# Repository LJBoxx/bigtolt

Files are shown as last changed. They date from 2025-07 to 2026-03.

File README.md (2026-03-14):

# BigTOLT - Big(kinda) esc with TOLT mosfets

18 mosfet TOLT package esc design based off vesc6 schematic and compatible with [VESC](https://github.com/vedderb/bldc) firmware.

There is also a small high voltage converter used for higher voltage operation, aim was to have a quite big voltage operation range. But if you will test it with high voltage, please do mind that the voltage sensing is **un-isolated**

# Untested !!
This board is not tested but the pcb is ready for prototype. BOM and gerber are in [here](/tolt)

## Board preview
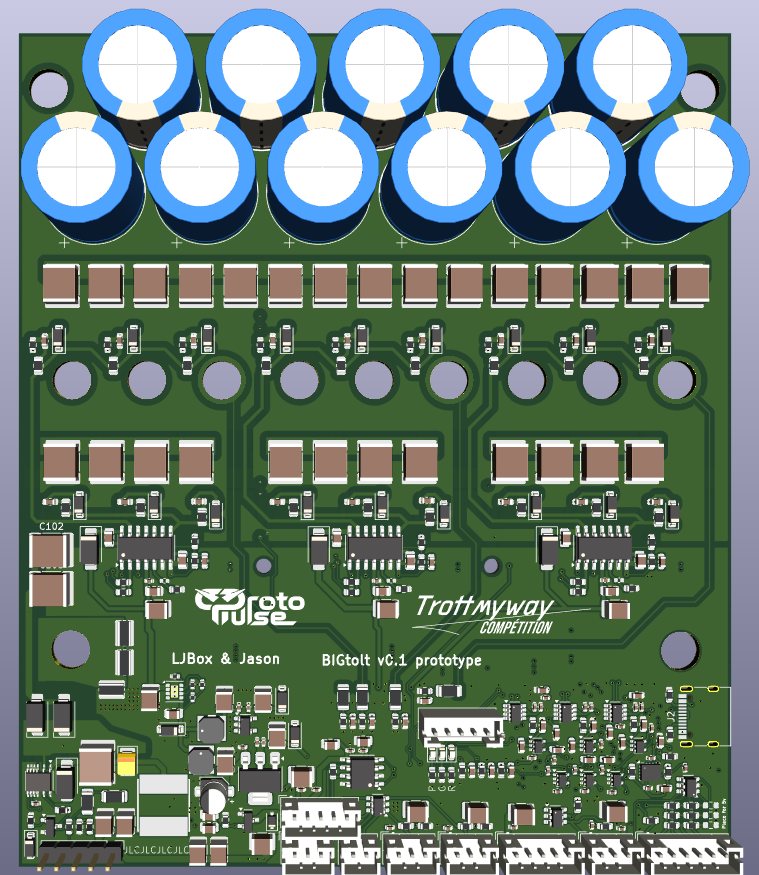
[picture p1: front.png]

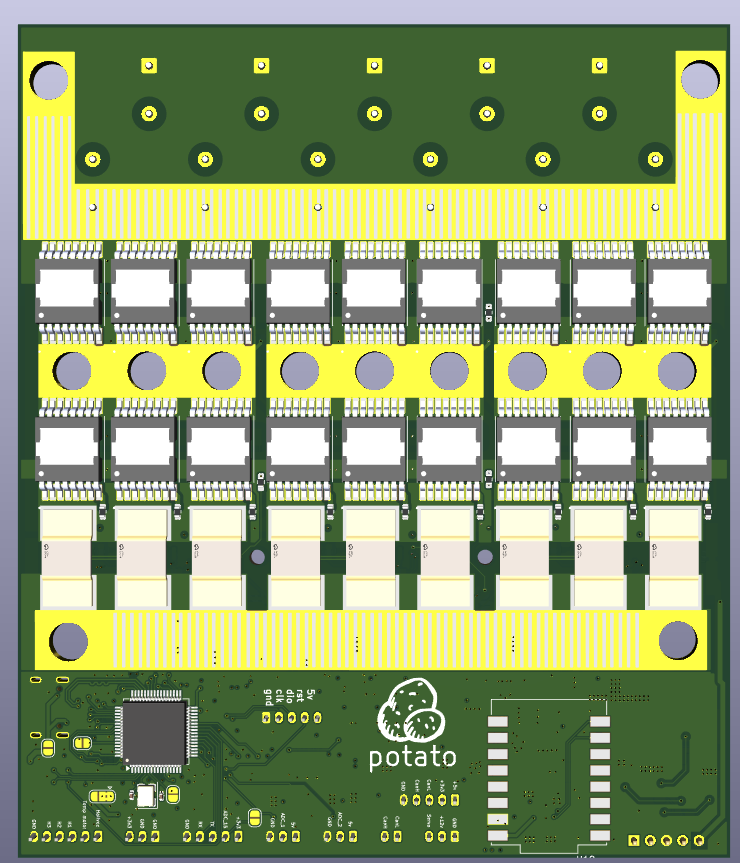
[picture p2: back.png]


## Liability
This project sources are provided **as is** therfore I, and the co controbutors to this repository shall not be held responsible for any damage occured, including but not limited to hardware damages or other physical injury caused by the outcomes of this source. **You are responsible for your actions. If used wrong, it will go wrong!**

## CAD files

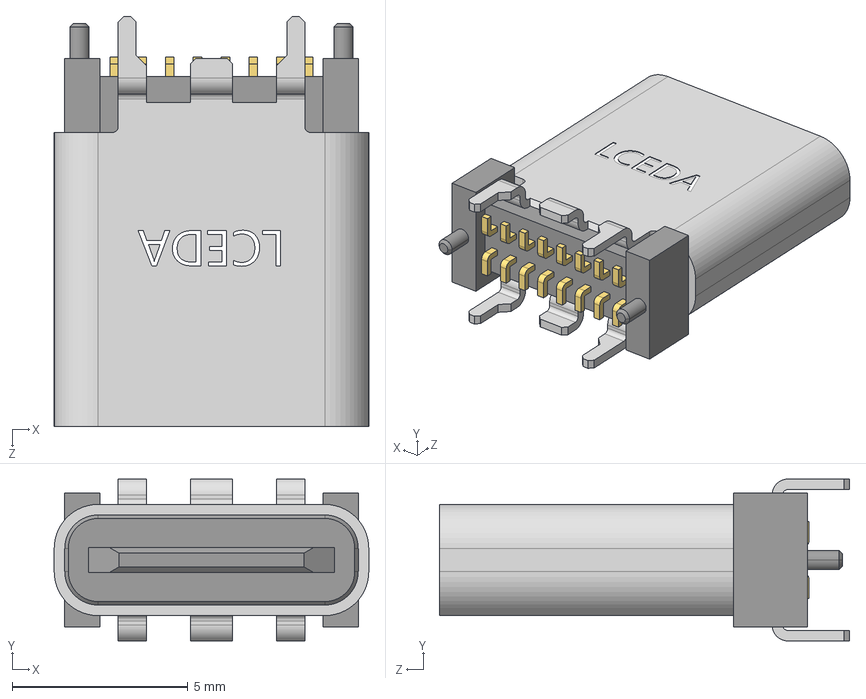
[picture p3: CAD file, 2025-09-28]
tolt/3d/USB-C-SMD_GT-USB-7051A.step
8.94 x 4.60 x 11.7 mm

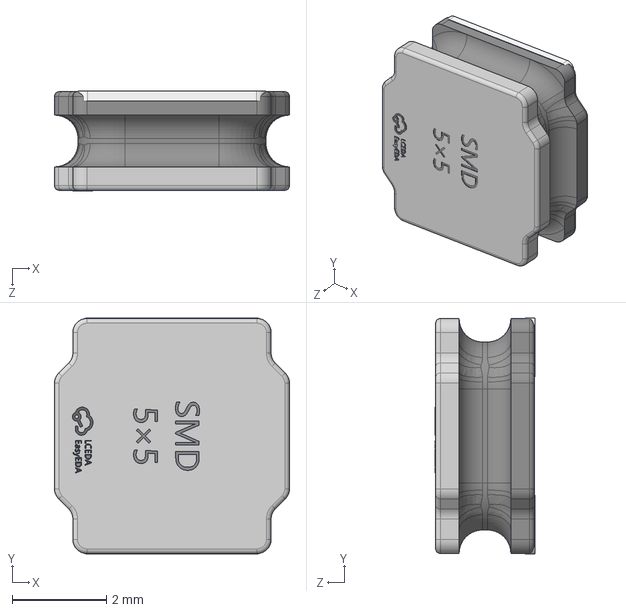
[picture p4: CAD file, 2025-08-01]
tolt/3d/IND-SMD_L5.0-W5.0-H2.1.step
5.00 x 5.02 x 2.12 mm

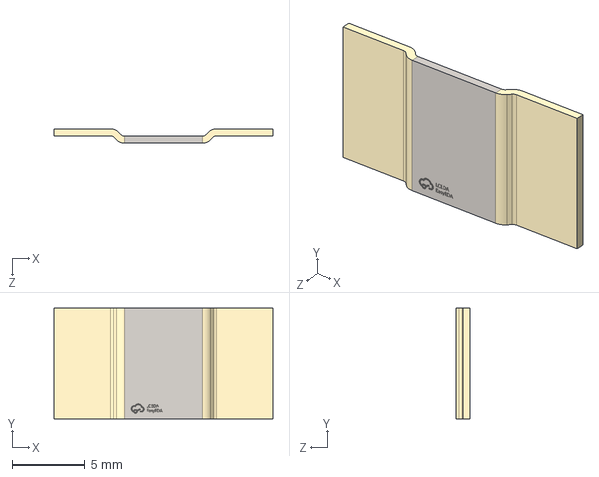
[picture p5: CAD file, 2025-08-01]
tolt/3d/R5930.step
15.0 x 7.60 x 0.981 mm

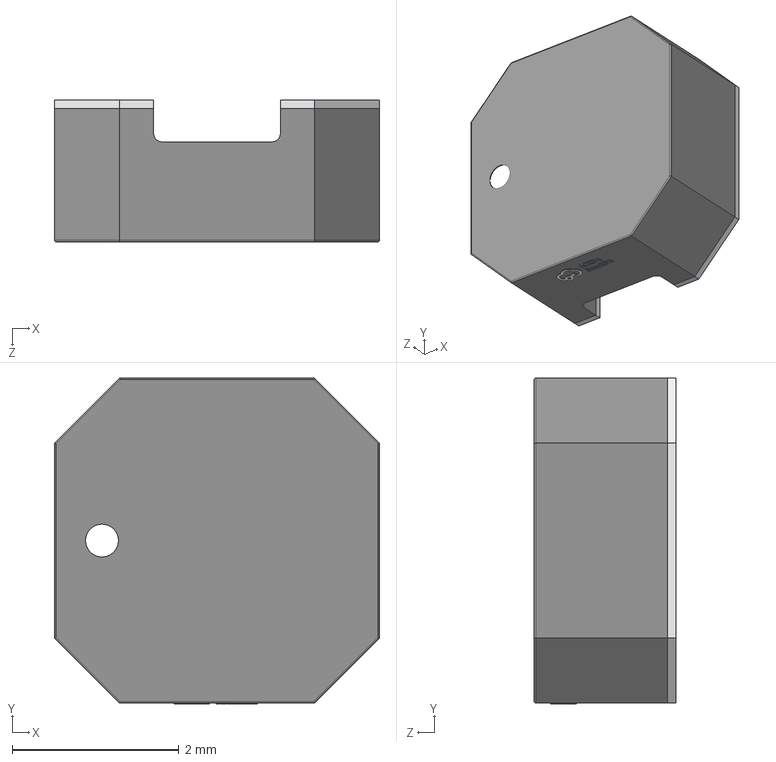
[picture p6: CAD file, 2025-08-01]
tolt/3d/IND-SMD_L3.9-W3.9-1.step
3.90 x 3.91 x 1.70 mm

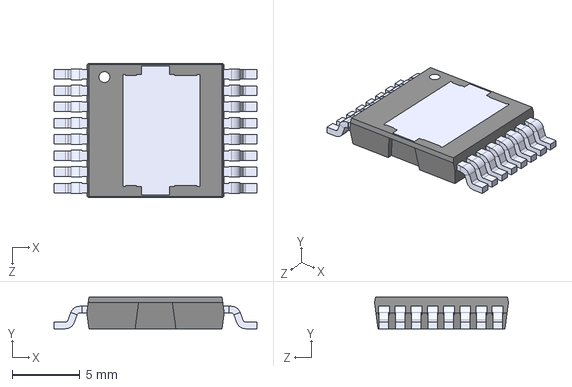
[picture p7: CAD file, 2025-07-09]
tolt/3d/SOP120P1500X235-17N.step
15.0 x 2.35 x 9.90 mm

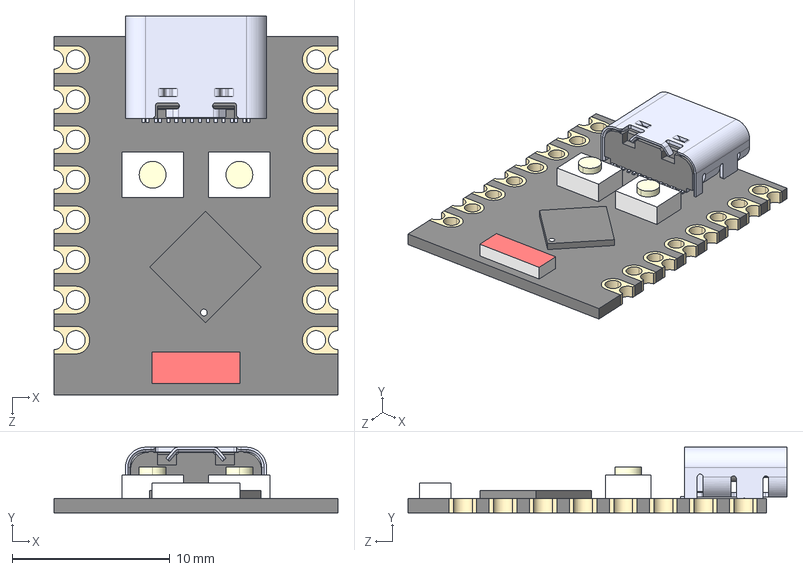
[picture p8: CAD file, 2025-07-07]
tolt/3d/ESP32-C3_SUPERMINI_SMD.step
18.0 x 4.16 x 24.0 mm
Board c3mini
USB C
components (other)^ESP32-C3 SuperMini

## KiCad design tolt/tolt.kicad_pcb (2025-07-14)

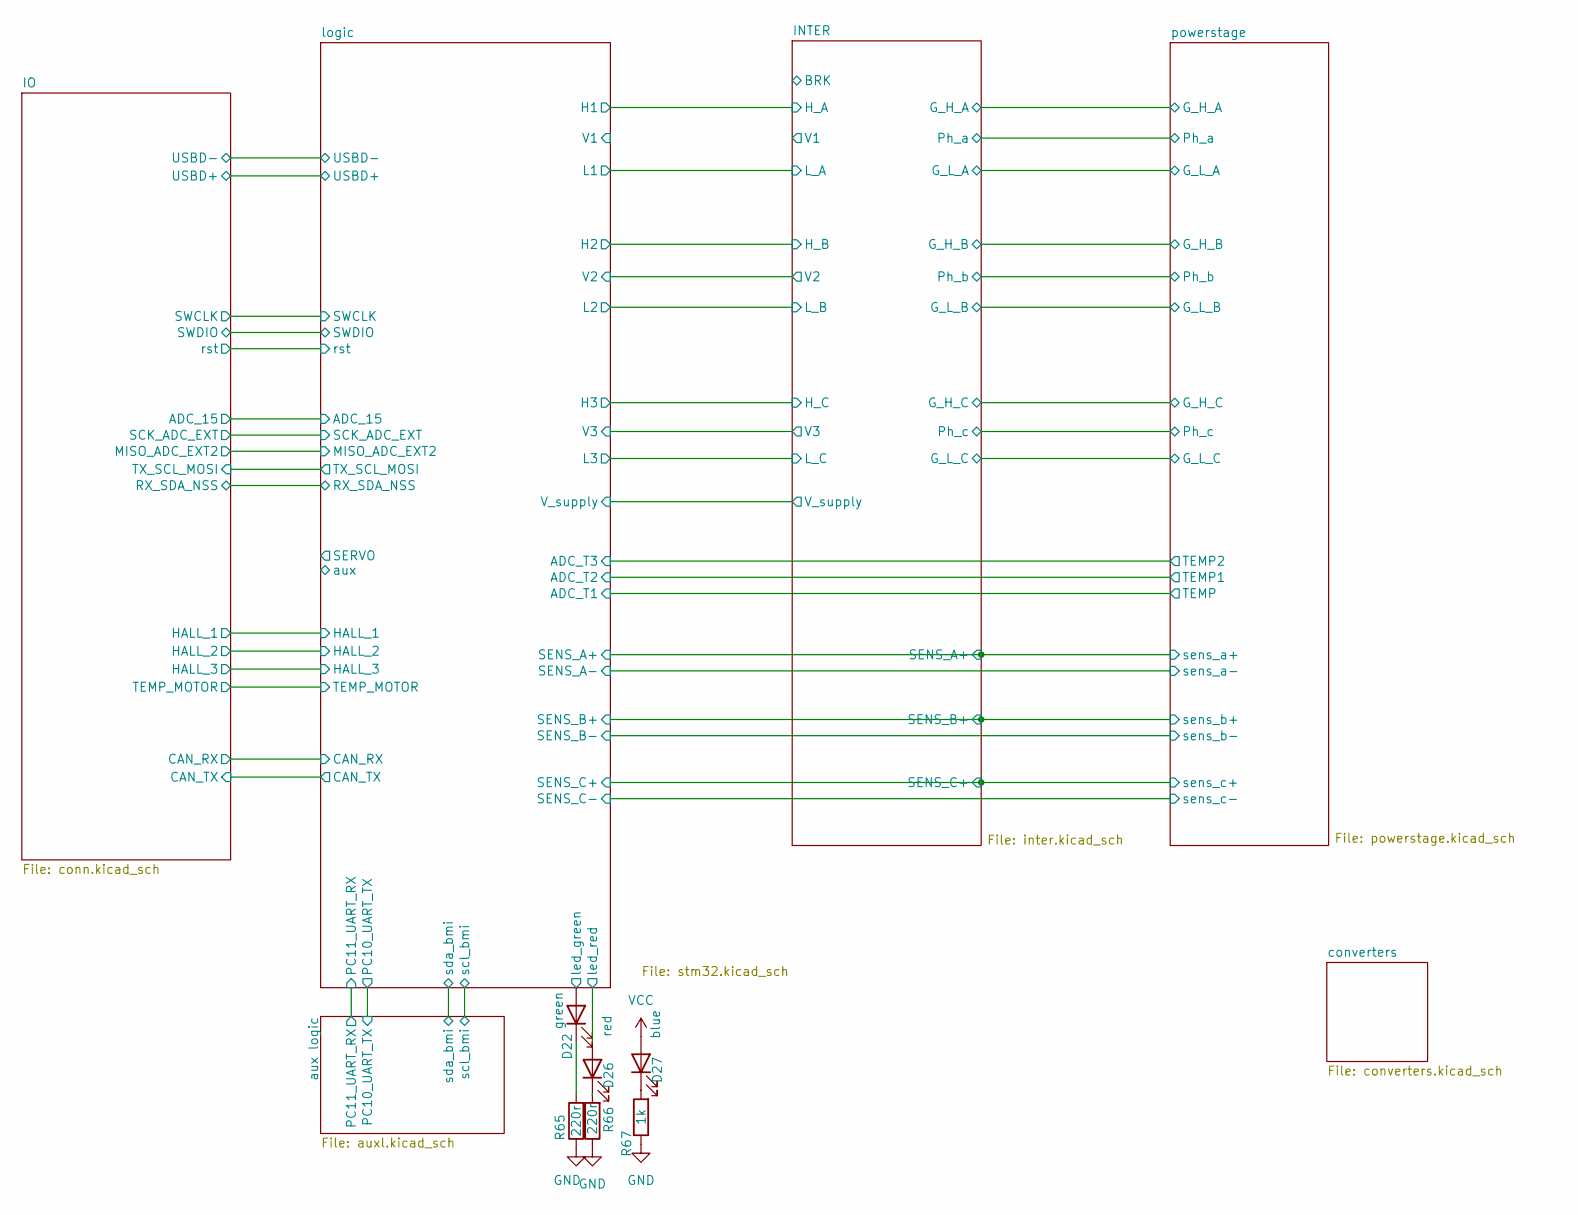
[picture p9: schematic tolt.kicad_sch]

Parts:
D22: green; D_0603_1608Metric_Pad1.05x0.95mm_HandSolder
D26: red; D_0603_1608Metric_Pad1.05x0.95mm_HandSolder
D27: blue; D_0603_1608Metric_Pad1.05x0.95mm_HandSolder
R65, R66: 220r; R_0603_1608Metric
R67: 1k; R_0603_1608Metric

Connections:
/logic/led_green: D22.2 (A); also elsewhere on the board
/logic/led_red: D26.2 (A); also elsewhere on the board
GND: R65.1, R66.1, R67.1; also elsewhere on the board
unnamed: D22.1 (K), R65.2
unnamed: D26.1 (K), R66.2
unnamed: D27.1 (K), R67.2
VCC: D27.2 (A); also elsewhere on the board

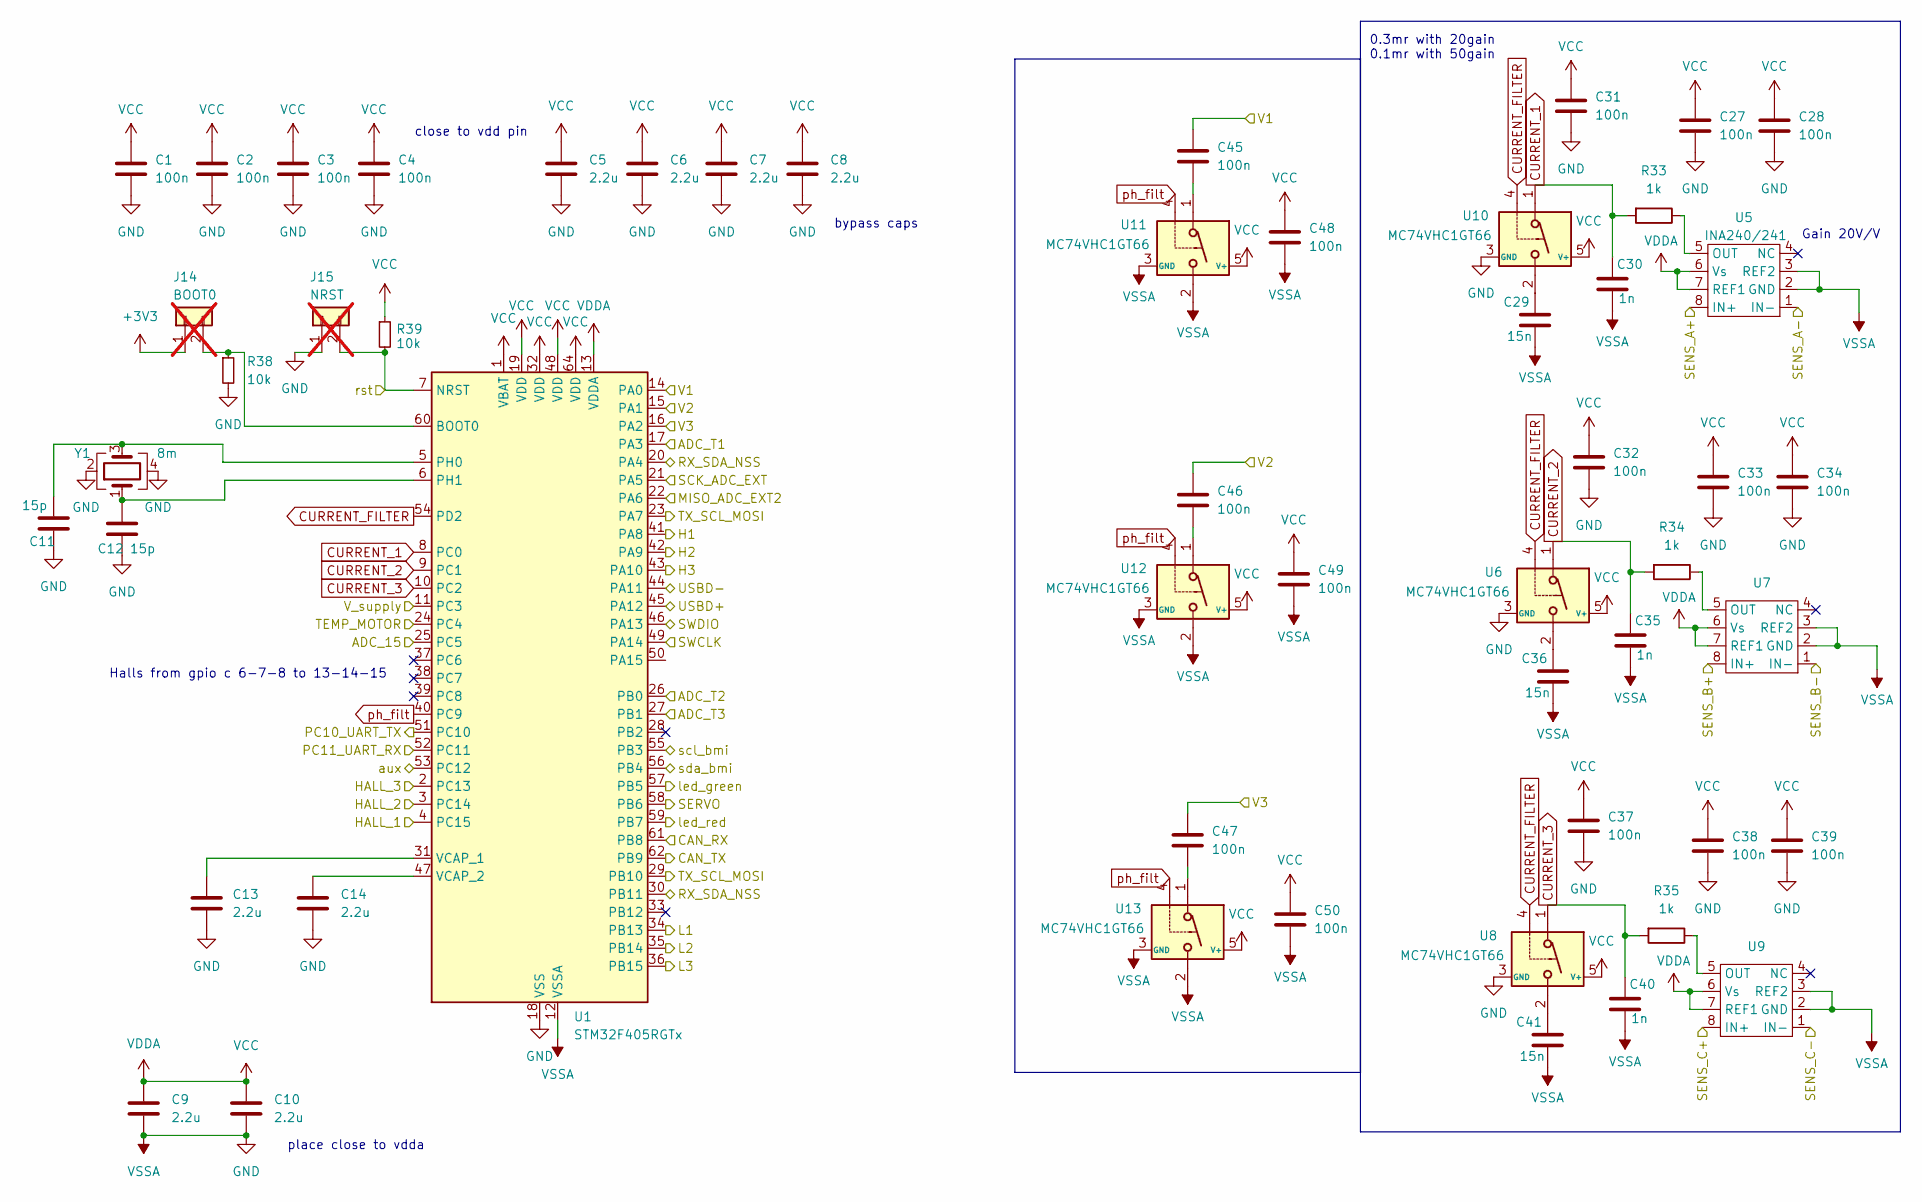
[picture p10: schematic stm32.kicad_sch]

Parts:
C1, C2, C3, C4, C27, C28, C31, C32, C33, C34, C37, C38, C39, C45, C46, C47, C48, C49, C50: 100n; C_0402_1005Metric
C5, C6, C7, C8, C9, C10, C13, C14: 2.2u; C_0603_1608Metric
C11, C12: 15p; C_0402_1005Metric
C29, C36, C41: 15n; C_0603_1608Metric
C30, C35, C40: 1n; C_0603_1608Metric
J14: BOOT0; SolderJumper-2_P1.3mm_Open_RoundedPad1.0x1.5mm; not fitted
J15: NRST; SolderJumper-2_P1.3mm_Open_RoundedPad1.0x1.5mm; not fitted
R33, R34, R35: 1k; R_0603_1608Metric
R38, R39: 10k; R_0603_1608Metric; LCSC C25804
U1: STM32F405RGTx; LQFP-64_10x10mm_P0.5mm
U5: INA240/241; SOT-23-8
U6, U8, U10, U11, U12, U13: MC74VHC1GT66; SOT-353_SC-70-5
U7, U9: SOT-23-8
Y1: 8m; Crystal_SMD_3225-4Pin_3.2x2.5mm

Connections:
+3V3: J14.1
/INTER/H_A: U1.41 (PA8); also elsewhere on the board
/INTER/H_B: U1.42 (PA9); also elsewhere on the board
/INTER/H_C: U1.43 (PA10); also elsewhere on the board
/INTER/L_A: U1.34 (PB13); also elsewhere on the board
/INTER/L_B: U1.35 (PB14); also elsewhere on the board
/INTER/L_C: U1.36 (PB15); also elsewhere on the board
/INTER/SENS_A+: U5.8 (IN+); also elsewhere on the board
/INTER/SENS_B+: U7.8 (IN+); also elsewhere on the board
/INTER/SENS_C+: U9.8 (IN+); also elsewhere on the board
/INTER/V2: C46.2, U1.15 (PA1); also elsewhere on the board
/INTER/V3: C47.2, U1.16 (PA2); also elsewhere on the board
/INTER/V_supply: U1.11 (PC3); also elsewhere on the board
/IO/ADC_15: U1.25 (PC5); also elsewhere on the board
/IO/CAN_RX: U1.61 (PB8); also elsewhere on the board
/IO/CAN_TX: U1.62 (PB9); also elsewhere on the board
/IO/HALL_1: U1.4 (PC15); also elsewhere on the board
/IO/HALL_2: U1.3 (PC14); also elsewhere on the board
/IO/HALL_3: U1.2 (PC13); also elsewhere on the board
/IO/MISO_ADC_EXT2: U1.22 (PA6); also elsewhere on the board
/IO/RX_SDA_NSS: U1.20 (PA4), U1.30 (PB11); also elsewhere on the board
/IO/SCK_ADC_EXT: U1.21 (PA5); also elsewhere on the board
/IO/SWCLK: U1.49 (PA14); also elsewhere on the board
/IO/SWDIO: U1.46 (PA13); also elsewhere on the board
/IO/TEMP_MOTOR: U1.24 (PC4); also elsewhere on the board
/IO/TX_SCL_MOSI: U1.23 (PA7), U1.29 (PB10); also elsewhere on the board
/IO/USBD+: U1.45 (PA12); also elsewhere on the board
/IO/USBD-: U1.44 (PA11); also elsewhere on the board
/IO/rst: J15.2, R39.2, U1.7 (NRST); also elsewhere on the board
/aux logic/PC10_UART_TX: U1.51 (PC10); also elsewhere on the board
/aux logic/PC11_UART_RX: U1.52 (PC11); also elsewhere on the board
/aux logic/scl_bmi: U1.55 (PB3); also elsewhere on the board
/aux logic/sda_bmi: U1.56 (PB4); also elsewhere on the board
/logic/ADC_T1: U1.17 (PA3); also elsewhere on the board
/logic/ADC_T2: U1.26 (PB0); also elsewhere on the board
/logic/ADC_T3: U1.27 (PB1); also elsewhere on the board
/logic/SERVO: U1.58 (PB6)
/logic/V1: C45.2, U1.14 (PA0)
/logic/aux: U1.53 (PC12)
/logic/led_green: U1.57 (PB5); also elsewhere on the board
/logic/led_red: U1.59 (PB7); also elsewhere on the board
CURRENT_1: C30.1, R33.2, U1.8 (PC0), U10.1
CURRENT_2: C35.1, R34.2, U1.9 (PC1), U6.1
CURRENT_3: C40.1, R35.2, U1.10 (PC2), U8.1
CURRENT_FILTER: U1.54 (PD2), U6.4, U8.4, U10.4
GND: C1.1, C2.1, C3.1, C4.1, C5.1, C6.1, C7.1, C8.1, C9.1, C10.1, C11.2, C12.2, C13.1, C14.1, C27.1, C28.1, C29.2, C30.2, C31.1, C32.1, C33.1, C34.1, C35.2, C36.2, C37.1, C38.1, C39.1, C40.2, C41.2, C48.1, C49.1, C50.1, J15.1, R38.2, U1.12 (VSSA), U1.18 (VSS), U1.63 (VSS), U5.2 (GND), U5.3 (REF2), U6.3 (GND), U7.2 (GND), U7.3 (REF2), U8.3 (GND), U9.2 (GND), U9.3 (REF2), U10.3 (GND), U11.2, U11.3 (GND), U12.2, U12.3 (GND), U13.2, U13.3 (GND), Y1.2, Y1.4; also elsewhere on the board
GNDPWR: U5.1 (IN-), U7.1 (IN-), U9.1 (IN-); also elsewhere on the board
unnamed: C29.1, U10.2
unnamed: C36.1, U6.2
unnamed: C41.1, U8.2
unnamed: C45.1, U11.1
unnamed: C46.1, U12.1
unnamed: C47.1, U13.1
unnamed: J14.2, R38.1, U1.60 (BOOT0)
unnamed: C11.1, U1.5 (PH0), Y1.3
unnamed: C12.1, U1.6 (PH1), Y1.1
unnamed: C13.2, U1.31 (VCAP_1)
unnamed: C14.2, U1.47 (VCAP_2)
unnamed: R33.1, U5.5 (OUT)
unnamed: R34.1, U7.5 (OUT)
unnamed: R35.1, U9.5 (OUT)
VCC: C1.2, C2.2, C3.2, C4.2, C5.2, C6.2, C7.2, C8.2, C9.2, C10.2, C27.2, C28.2, C31.2, C32.2, C33.2, C34.2, C37.2, C38.2, C39.2, C48.2, C49.2, C50.2, R39.1, U1.1 (VBAT), U1.13 (VDDA), U1.19 (VDD), U1.32 (VDD), U1.48 (VDD), U1.64 (VDD), U5.6 (Vs), U5.7 (REF1), U6.5 (V+), U7.6 (Vs), U7.7 (REF1), U8.5 (V+), U9.6 (Vs), U9.7 (REF1), U10.5 (V+), U11.5 (V+), U12.5 (V+), U13.5 (V+); also elsewhere on the board
ph_filt: U1.40 (PC9), U11.4, U12.4, U13.4

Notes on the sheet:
close to vdd pin
0.3mr with 20gain 0.1mr with 50gain
place close to vdda
Gain 20V/V
Halls from gpio c 6-7-8 to 13-14-15
bypass caps

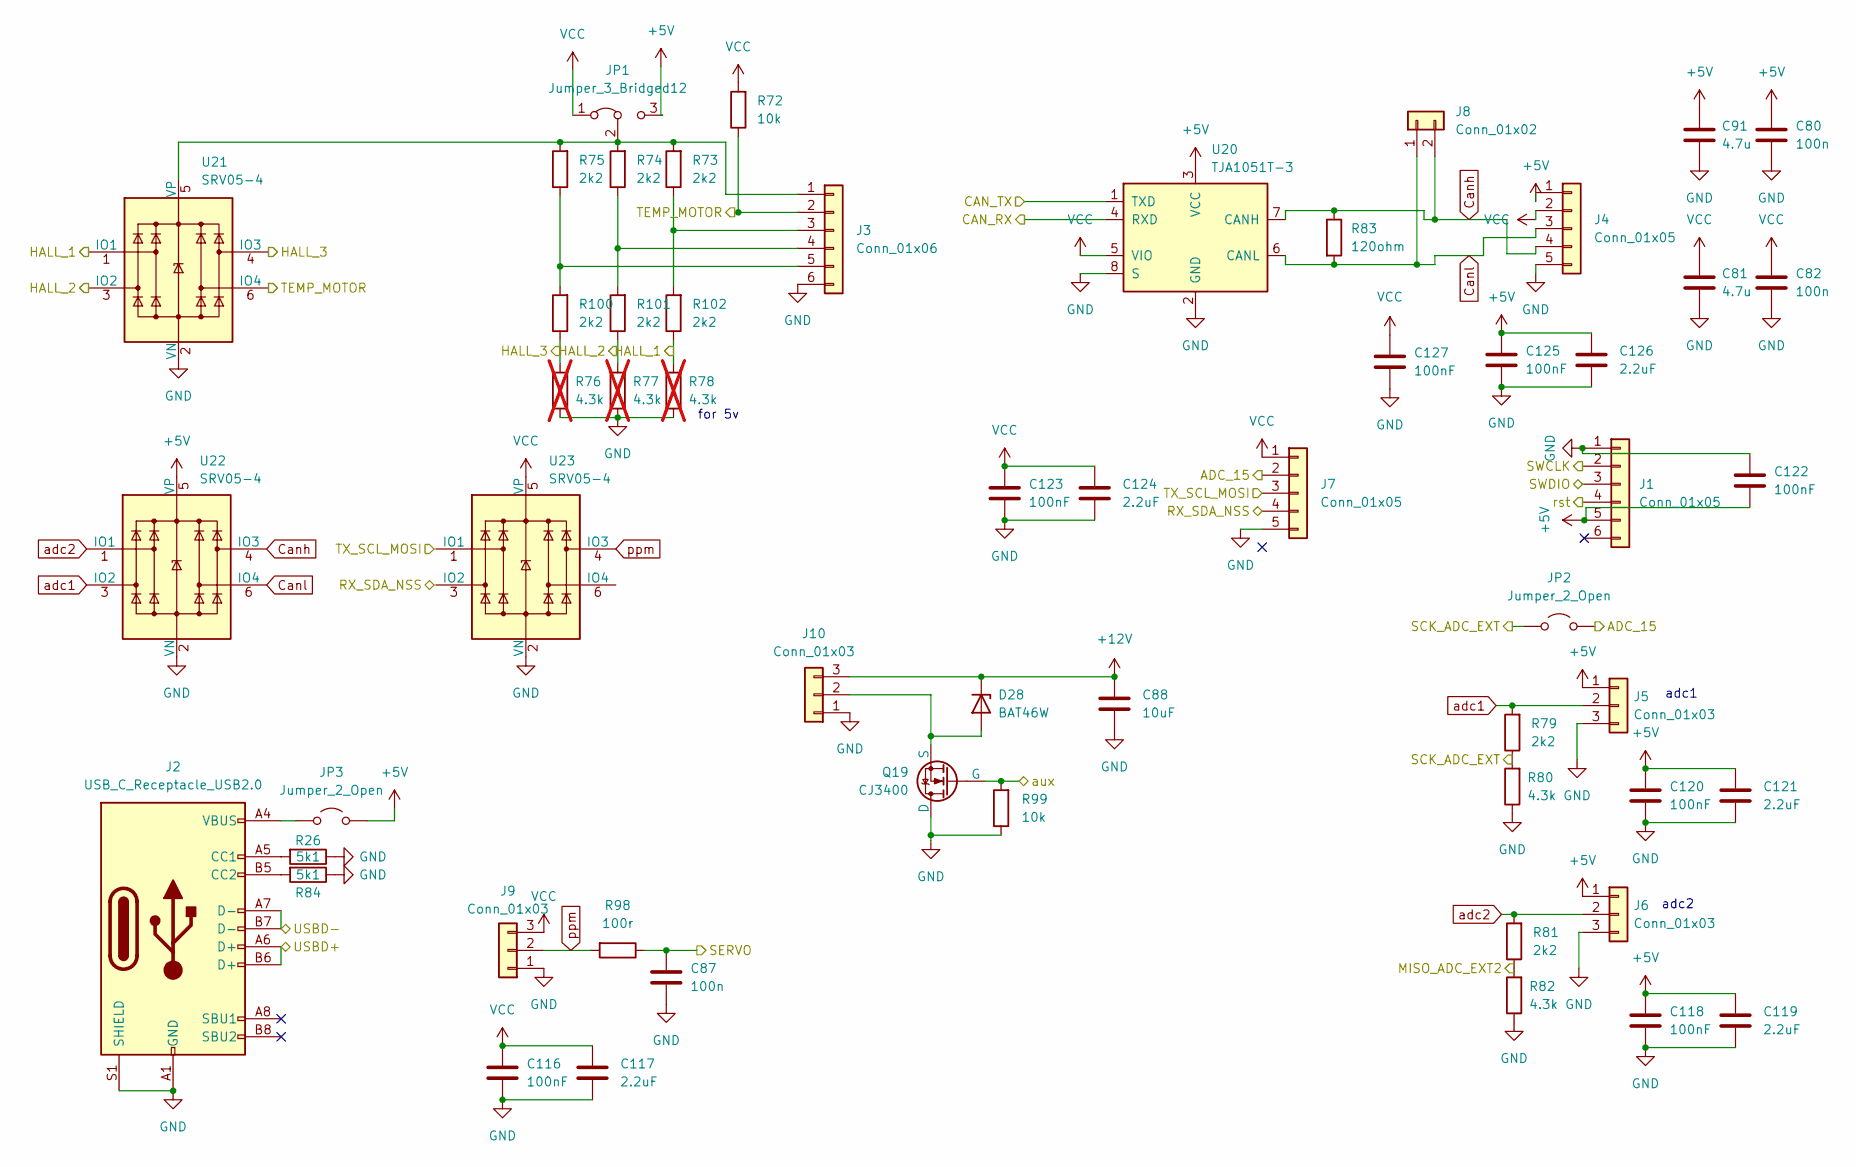
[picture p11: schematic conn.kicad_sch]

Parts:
C80, C82, C87: 100n; C_0402_1005Metric
C81, C91: 4.7u; C_0805_2012Metric
C88: 10uF; C_1210_3225Metric
C116, C118, C120, C122, C123, C125, C127: 100nF; C_0402_1005Metric
C117, C119, C121, C124, C126: 2.2uF; C_1210_3225Metric
D28: BAT46W; D_SOD-323F
J1: Conn_01x05; PinSocket_2x03_P2.54mm_Vertical
J2: USB_C_Receptacle_USB2.0; USB_C_Receptacle_G-Switch_GT-USB-7051x
J3: Conn_01x06; JST_PH_B6B-PH-K_1x06_P2.00mm_Vertical
J4, J7: Conn_01x05; JST_PH_B5B-PH-K_1x05_P2.00mm_Vertical
J5, J6, J9, J10: Conn_01x03; JST_PH_B3B-PH-K_1x03_P2.00mm_Vertical
J8: Conn_01x02; JST_PH_B2B-PH-K_1x02_P2.00mm_Vertical
JP1: Jumper_3_Bridged12; SolderJumper-3_P1.3mm_Bridged2Bar12_RoundedPad1.0x1.5mm
JP2, JP3: Jumper_2_Open; SolderJumper-2_P1.3mm_Open_RoundedPad1.0x1.5mm
Q19: CJ3400; SOT-23_Handsoldering
R26, R84: 5k1; R_0603_1608Metric
R72, R99: 10k; R_0603_1608Metric
R73, R74, R75, R79, R81, R100, R101, R102: 2k2; R_0603_1608Metric
R76, R77, R78: 4.3k; R_0603_1608Metric; not fitted
R80, R82: 4.3k; R_0603_1608Metric
R83: 120ohm; R_0603_1608Metric
R98: 100r; R_0603_1608Metric
U20: TJA1051T-3; SOIC-8_3.9x4.9mm_P1.27mm
U21, U22, U23: SRV05-4; SOT-23-6

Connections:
+5V: C80.2, C91.2, C118.1, C119.1, C120.1, C121.1, C122.2, C125.1, C126.1, J1.5, J4.1, J5.1, J6.1, JP1.3 (B), JP3.2 (B), U20.3 (VCC), U22.5 (VP); also elsewhere on the board
+12V: C88.2, D28.1 (K), J10.3; also elsewhere on the board
/IO/ADC_15: J7.2, JP2.2 (B); also elsewhere on the board
/IO/CAN_RX: U20.4 (RXD); also elsewhere on the board
/IO/CAN_TX: U20.1 (TXD); also elsewhere on the board
/IO/HALL_1: R78.2, R102.1, U21.1 (IO1); also elsewhere on the board
/IO/HALL_2: R77.2, R101.1, U21.3 (IO2); also elsewhere on the board
/IO/HALL_3: R76.2, R100.1, U21.4 (IO3); also elsewhere on the board
/IO/MISO_ADC_EXT2: R81.1, R82.2; also elsewhere on the board
/IO/RX_SDA_NSS: J7.4; also elsewhere on the board
/IO/SCK_ADC_EXT: JP2.1 (A), R79.1, R80.2; also elsewhere on the board
/IO/SERVO: C87.2, R98.1
/IO/SWCLK: J1.2; also elsewhere on the board
/IO/SWDIO: J1.3; also elsewhere on the board
/IO/TEMP_MOTOR: J3.2, R72.1, U21.6 (IO4); also elsewhere on the board
/IO/TX_SCL_MOSI: J7.3; also elsewhere on the board
/IO/USBD+: J2.A6 (D+), J2.B6 (D+); also elsewhere on the board
/IO/USBD-: J2.A7 (D-), J2.B7 (D-); also elsewhere on the board
/IO/aux: Q19.2 (G), R99.2
/IO/rst: J1.4; also elsewhere on the board
Canh: J4.4, J8.2, R83.1, U20.7 (CANH), U22.4 (IO3)
Canl: J4.3, J8.1, R83.2, U20.6 (CANL), U22.6 (IO4)
GND: C80.1, C81.1, C82.1, C87.1, C88.1, C91.1, C116.2, C117.2, C118.2, C119.2, C120.2, C121.2, C122.1, C123.2, C124.2, C125.2, C126.2, C127.2, J1.1, J2.A1 (GND), J2.A12 (GND), J2.B1 (GND), J2.B12 (GND), J2.S1 (SHIELD), J3.6, J4.5, J5.3, J6.3, J7.5, J9.1, J10.1, Q19.1 (D), R26.1, R76.1, R77.1, R78.1, R80.1, R82.1, R84.1, R99.1, U20.2 (GND), U20.8 (S), U21.2 (VN), U22.2 (VN), U23.2 (VN); also elsewhere on the board
unnamed: D28.2 (A), J10.2, Q19.3 (S)
unnamed: J2.A5 (CC1), R26.2
unnamed: J2.B5 (CC2), R84.2
unnamed: J3.1, JP1.2 (C), R73.2, R74.2, R75.2, U21.5 (VP)
unnamed: J3.3, R73.1, R102.2
unnamed: J3.4, R74.1, R101.2
unnamed: J3.5, R75.1, R100.2
unnamed: J2.A4 (VBUS), J2.A9 (VBUS), J2.B4 (VBUS), J2.B9 (VBUS), JP3.1 (A)
VCC: C81.2, C82.2, C116.1, C117.1, C123.1, C124.1, C127.1, J4.2, J7.1, J9.3, JP1.1 (A), R72.2, U20.5 (VIO), U23.5 (VP); also elsewhere on the board
adc1: J5.2, R79.2, U22.3 (IO2)
adc2: J6.2, R81.2, U22.1 (IO1)
ppm: J9.2, R98.2, U23.4 (IO3)

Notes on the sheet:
adc2
adc1
for 5v

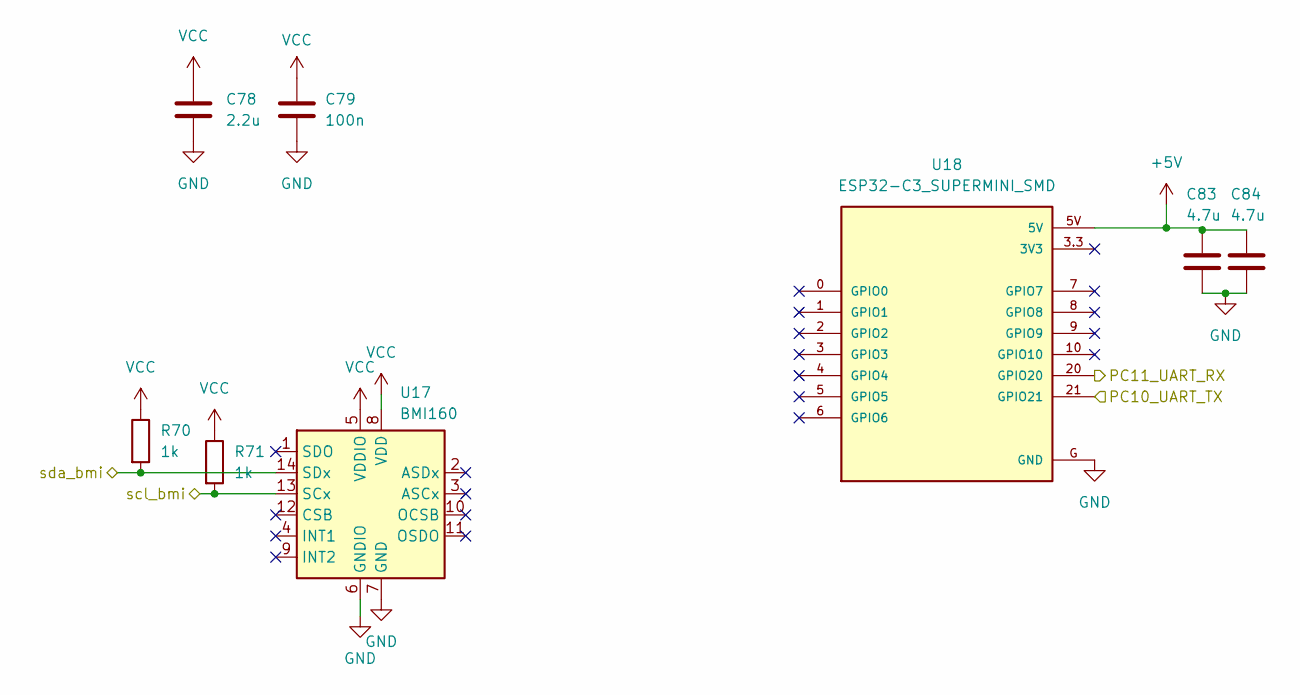
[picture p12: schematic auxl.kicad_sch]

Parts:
C78: 2.2u; C_0603_1608Metric
C79: 100n; C_0402_1005Metric
C83, C84: 4.7u; C_0805_2012Metric
R70, R71: 1k; R_0603_1608Metric
U17: BMI160; Bosch_LGA-14_3x2.5mm_P0.5mm
U18: ESP32-C3_SUPERMINI_SMD; MODULE_ESP32-C3_SUPERMINI

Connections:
+5V: C83.2, C84.2, U18.5V; also elsewhere on the board
/aux logic/PC10_UART_TX: U18.21 (GPIO21); also elsewhere on the board
/aux logic/PC11_UART_RX: U18.20 (GPIO20); also elsewhere on the board
/aux logic/scl_bmi: R71.2, U17.13 (SCx); also elsewhere on the board
/aux logic/sda_bmi: R70.2, U17.14 (SDx); also elsewhere on the board
GND: C78.1, C79.1, C83.1, C84.1, U17.6 (GNDIO), U17.7 (GND), U18.G (GND); also elsewhere on the board
VCC: C78.2, C79.2, R70.1, R71.1, U17.5 (VDDIO), U17.8 (VDD); also elsewhere on the board

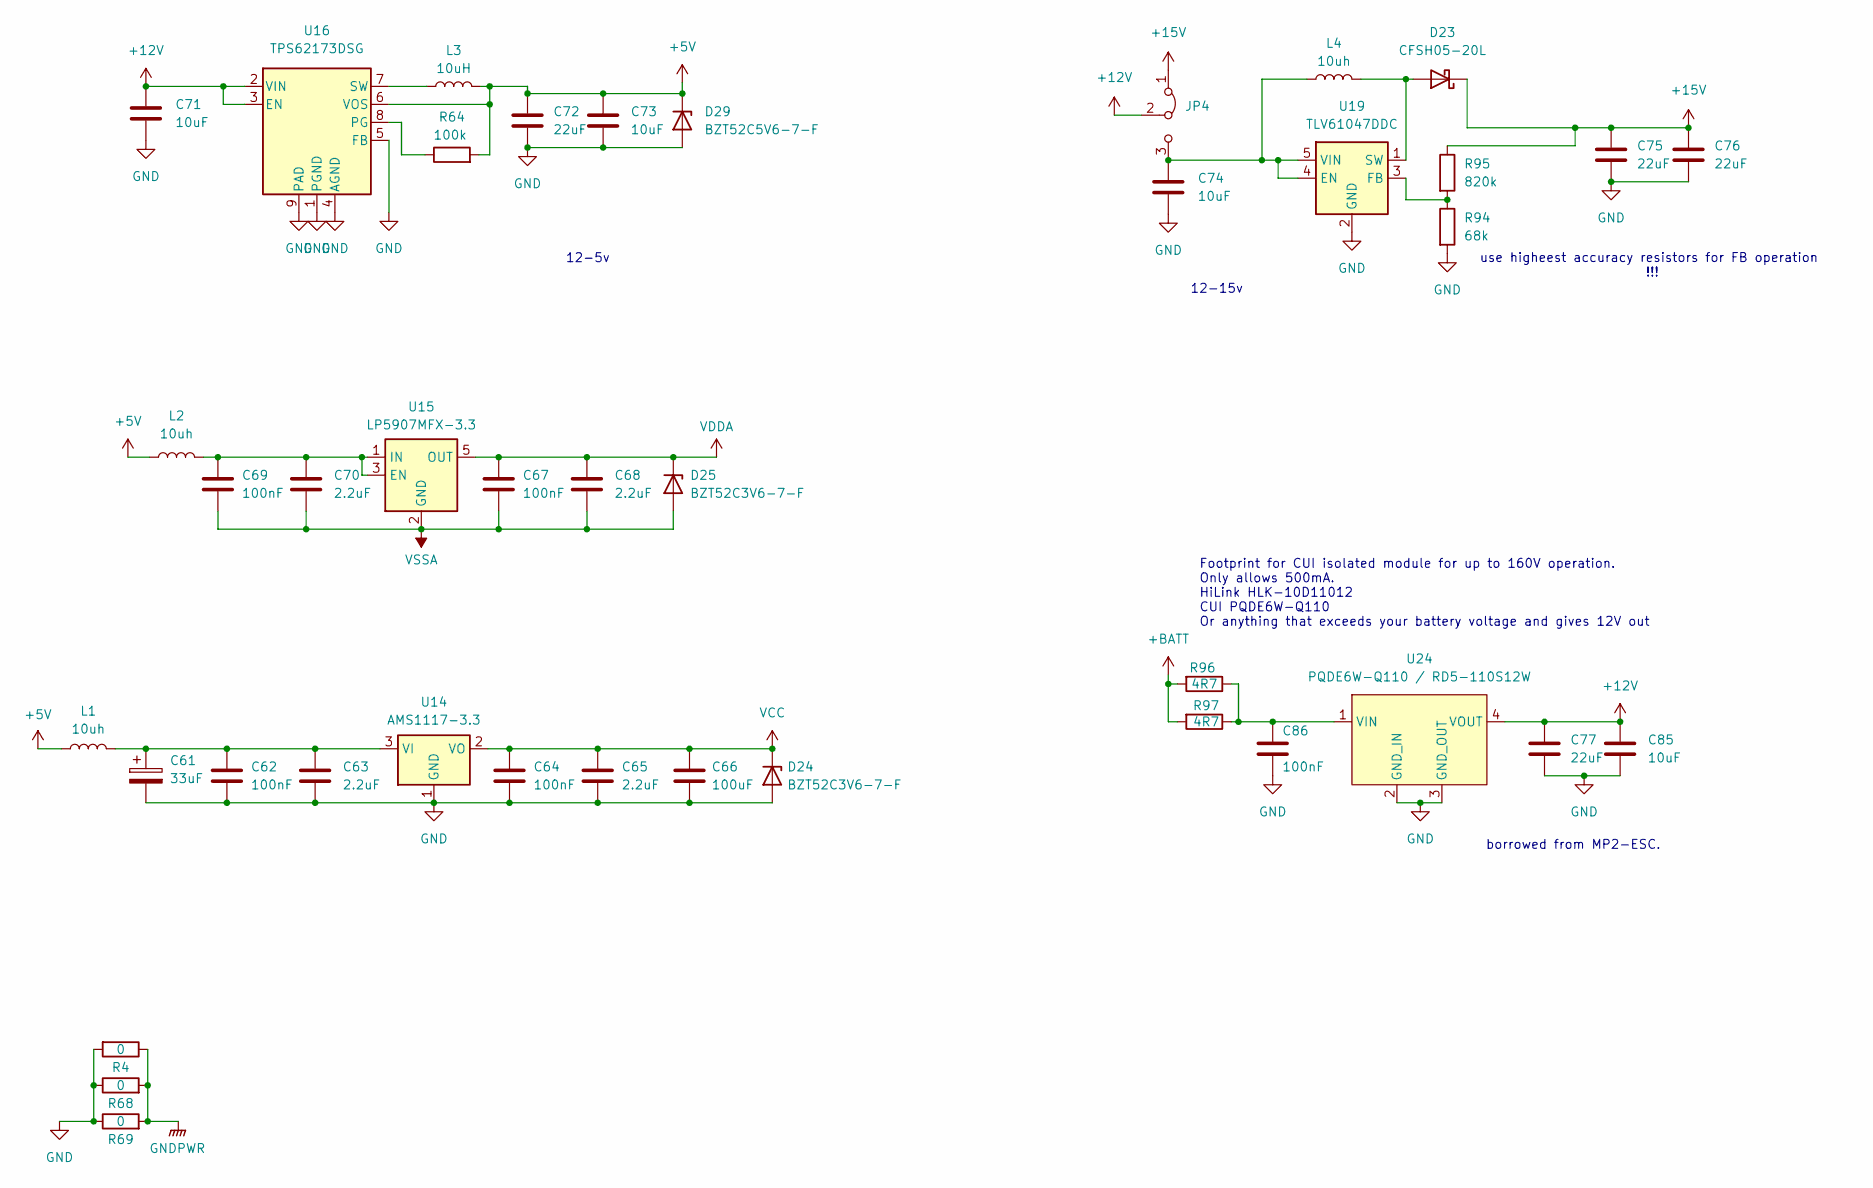
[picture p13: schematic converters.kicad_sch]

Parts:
C61: 33uF; CP_Elec_4x5.4
C62, C64, C67, C69: 100nF; C_0402_1005Metric
C63, C65, C68, C70: 2.2uF; C_1210_3225Metric
C66: 100uF; C_0402_1005Metric
C71, C73, C74, C85: 10uF; C_1210_3225Metric
C72, C75, C76, C77: 22uF; C_1210_3225Metric; part TAJB226K016RNJ
C86: 100nF; C_0805_2012Metric; LCSC C342865
D23: CFSH05-20L; D_SOD-882
D24, D25: BZT52C3V6-7-F; D_SOD-123
D29: BZT52C5V6-7-F; D_SOD-123
JP4: Jumper_3_Bridged12; SolderJumper-3_P1.3mm_Bridged2Bar12_RoundedPad1.0x1.5mm
L1, L2: 10uh; IND-SMD_L3.9-W3.9-1
L3: 10uH; IND-SMD_L5.0-W5.0
L4: 10uh; L_Abracon_ASPI-4030S
R4, R68, R69: 0; R_0815_2038Metric
R64: 100k; R_0603_1608Metric
R94: 68k; R_0603_1608Metric
R95: 820k; R_0603_1608Metric
R96, R97: 4R7; R_0805_2012Metric; LCSC C17675
U14: AMS1117-3.3; SOT-223-3_TabPin2
U15: LP5907MFX-3.3; SOT-23-5
U16: TPS62173DSG; WSON-8-1EP_2x2mm_P0.5mm_EP0.9x1.6mm
U19: TLV61047DDC; SOT-23-5
U24: PQDE6W-Q110 / RD5-110S12W; PQDE6W

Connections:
+5V: C72.2, C73.2, D29.1 (K), L1.1, L2.1, L3.2, R64.2, U16.6 (VOS); also elsewhere on the board
+12V: C71.2, C77.2, C85.2, JP4.2 (C), U16.2 (VIN), U16.3 (EN), U24.4 (VOUT); also elsewhere on the board
+15V: C75.2, C76.2, D23.1 (K), JP4.1 (A), R95.1; also elsewhere on the board
+BATT: R96.2, R97.2; also elsewhere on the board
GND: C61.2, C62.2, C63.2, C64.2, C65.2, C66.2, C67.2, C68.2, C69.2, C70.2, C71.1, C72.1, C73.1, C74.1, C75.1, C76.1, C77.1, C85.1, C86.2, D24.2 (A), D25.2 (A), D29.2 (A), R4.2, R68.1, R69.1, R94.2, U14.1 (GND), U15.2 (GND), U16.1 (PGND), U16.4 (AGND), U16.5 (FB), U16.9 (PAD), U19.2 (GND), U24.2 (GND_IN), U24.3 (GND_OUT); also elsewhere on the board
GNDPWR: R4.1, R68.2, R69.2; also elsewhere on the board
unnamed: D23.2 (A), L4.2, U19.1 (SW)
unnamed: C74.2, JP4.3 (B), L4.1, U19.4 (EN), U19.5 (VIN)
unnamed: C61.1, C62.1, C63.1, L1.2, U14.3 (VI)
unnamed: C69.1, C70.1, L2.2, U15.1 (IN), U15.3 (EN)
unnamed: R64.1, U16.8 (PG)
unnamed: L3.1, U16.7 (SW)
unnamed: R94.1, R95.2, U19.3 (FB)
unnamed: C86.1, R96.1, R97.1, U24.1 (VIN)
VCC: C64.1, C65.1, C66.1, C67.1, C68.1, D24.1 (K), D25.1 (K), U14.2 (VO), U15.5 (OUT); also elsewhere on the board

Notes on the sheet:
12-15v
Footprint for CUI isolated module for up to 160V operation. Only allows 500mA. HiLink HLK-10D11012 CUI PQDE6W-Q110 Or anything that exceeds your battery voltage and gives 12V out
borrowed from MP2-ESC.
12-5v
use higheest accuracy resistors for FB operation !!!

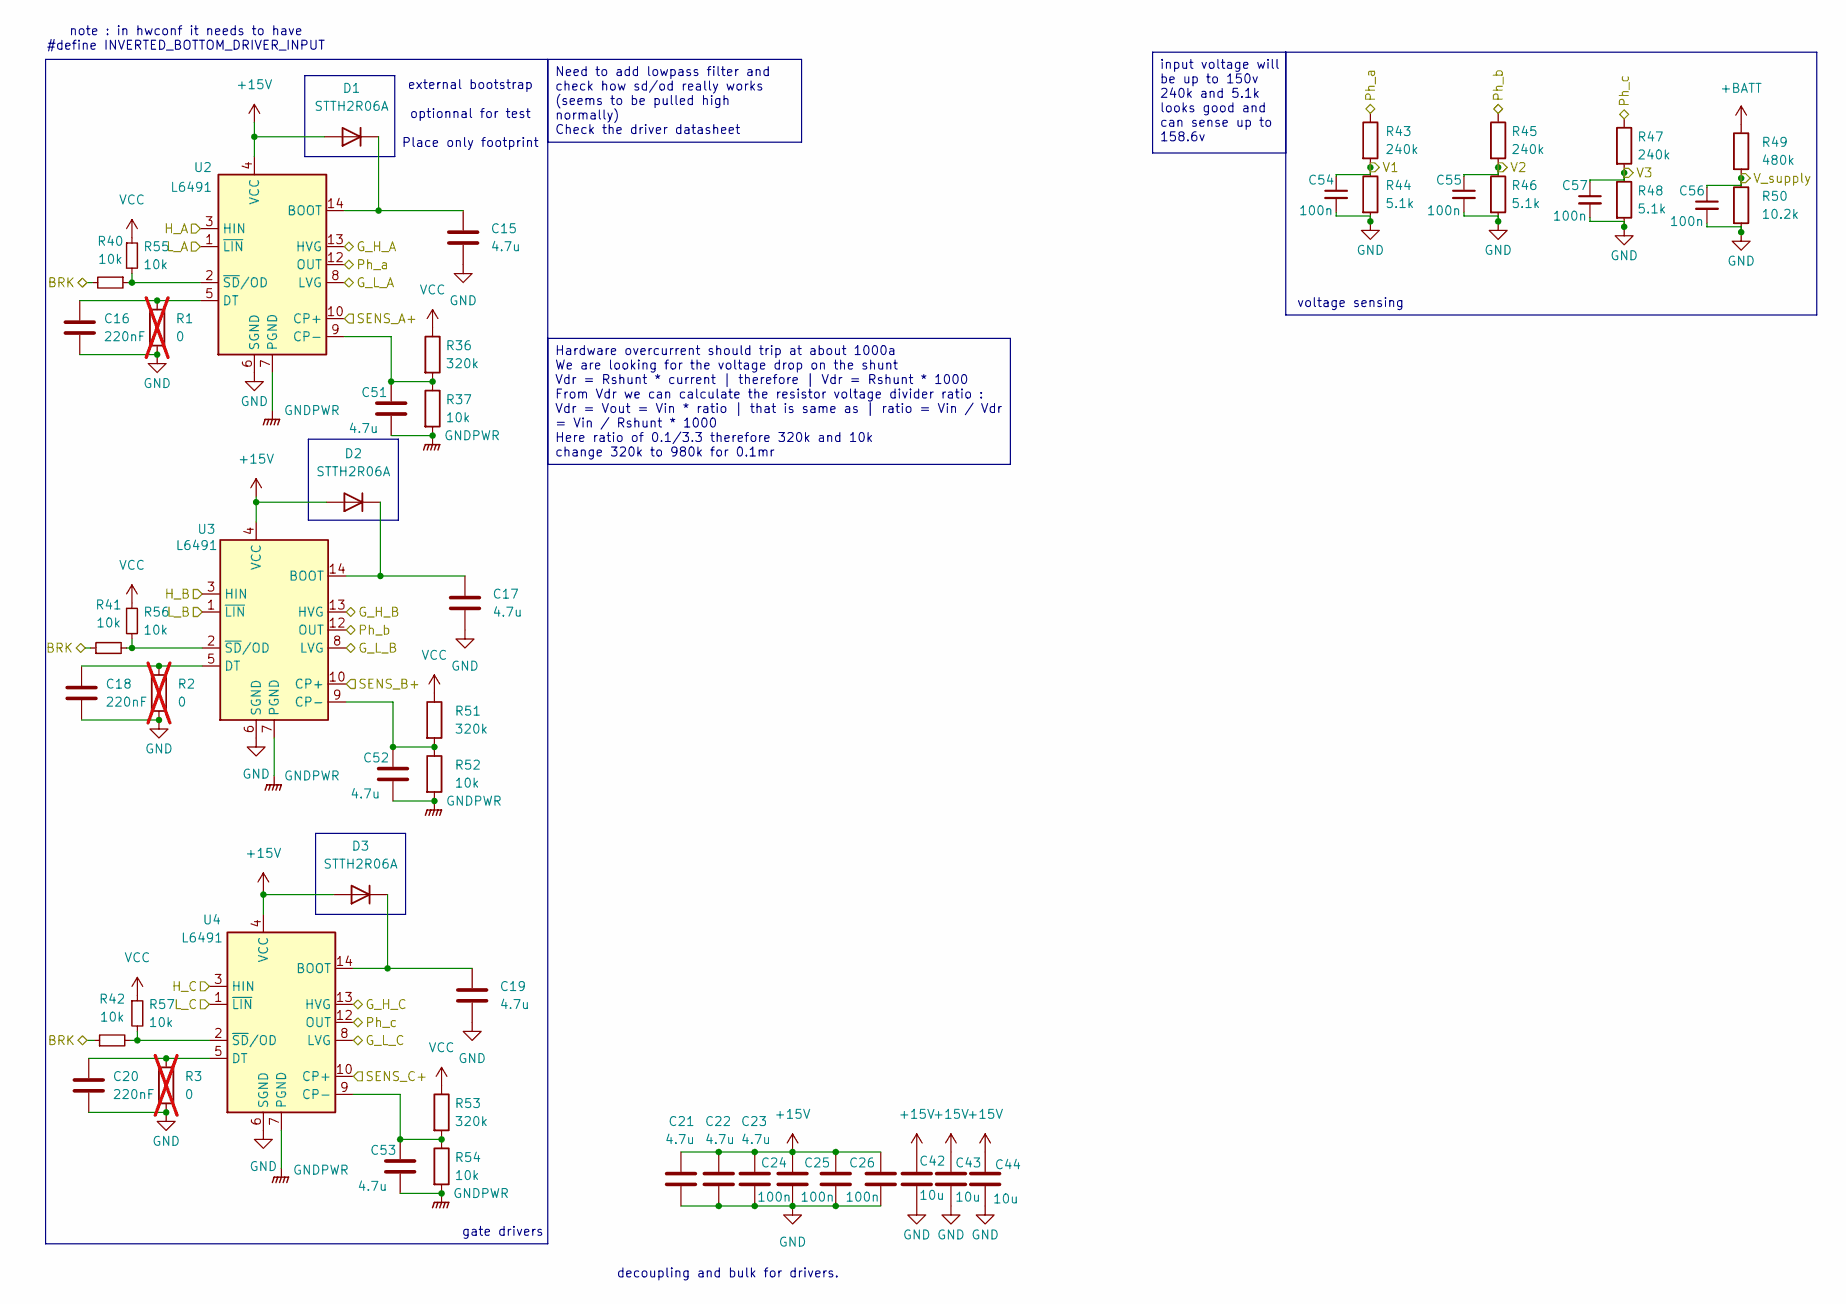
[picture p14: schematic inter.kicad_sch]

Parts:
C15, C17, C19, C21, C22, C23: 4.7u; C_0805_2012Metric
C16, C18, C20: 220nF; C_0402_1005Metric
C24, C25, C26: 100n; C_0402_1005Metric
C42, C43, C44: 10u; C_1210_3225Metric_Pad1.33x2.70mm_HandSolder
C51, C52, C53: 4.7u; C_0603_1608Metric
C54, C55, C56, C57: 100n; C_0603_1608Metric
D1, D2, D3: STTH2R06A; D_SMA
R1, R2, R3: 0; R_0603_1608Metric; not fitted
R36, R51, R53: 320k; R_0603_1608Metric
R37, R52, R54: 10k; R_0603_1608Metric
R40, R41, R42, R55, R56, R57: 10k; R_0603_1608Metric; LCSC C25804
R43, R45, R47: 240k; R_1206_3216Metric
R44, R46, R48: 5.1k; R_0603_1608Metric
R49: 480k; R_1206_3216Metric
R50: 10.2k; R_0603_1608Metric
U2, U3, U4: L6491; SO-14_3.9x8.65mm_P1.27mm

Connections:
+15V: C21.2, C22.2, C23.2, C24.2, C25.2, C26.2, C42.1, C43.1, C44.1, D1.2 (A), D2.2 (A), D3.2 (A), U2.4 (VCC), U3.4 (VCC), U4.4 (VCC); also elsewhere on the board
+BATT: R49.1; also elsewhere on the board
/INTER/BRK: R40.2, R41.1, R42.1
/INTER/G_H_A: U2.13 (HVG); also elsewhere on the board
/INTER/G_H_B: U3.13 (HVG); also elsewhere on the board
/INTER/G_H_C: U4.13 (HVG); also elsewhere on the board
/INTER/G_L_A: U2.8 (LVG); also elsewhere on the board
/INTER/G_L_B: U3.8 (LVG); also elsewhere on the board
/INTER/G_L_C: U4.8 (LVG); also elsewhere on the board
/INTER/H_A: U2.3 (HIN); also elsewhere on the board
/INTER/H_B: U3.3 (HIN); also elsewhere on the board
/INTER/H_C: U4.3 (HIN); also elsewhere on the board
/INTER/L_A: U2.1 (~LIN); also elsewhere on the board
/INTER/L_B: U3.1 (~LIN); also elsewhere on the board
/INTER/L_C: U4.1 (~LIN); also elsewhere on the board
/INTER/Ph_a: R43.1, U2.12 (OUT); also elsewhere on the board
/INTER/Ph_b: R45.1, U3.12 (OUT); also elsewhere on the board
/INTER/Ph_c: R47.1, U4.12 (OUT); also elsewhere on the board
/INTER/SENS_A+: U2.10 (CP+); also elsewhere on the board
/INTER/SENS_B+: U3.10 (CP+); also elsewhere on the board
/INTER/SENS_C+: U4.10 (CP+); also elsewhere on the board
/INTER/V1: C54.1, R43.2, R44.1
/INTER/V2: C55.1, R45.2, R46.1; also elsewhere on the board
/INTER/V3: C57.1, R47.2, R48.1; also elsewhere on the board
/INTER/V_supply: C56.1, R49.2, R50.1; also elsewhere on the board
GND: C15.2, C16.1, C17.2, C18.1, C19.2, C20.1, C21.1, C22.1, C23.1, C24.1, C25.1, C26.1, C42.2, C43.2, C44.2, C54.2, C55.2, C56.2, C57.2, R1.2, R2.2, R3.2, R44.2, R46.2, R48.2, R50.2, U2.6 (SGND), U3.6 (SGND), U4.6 (SGND); also elsewhere on the board
GNDPWR: C51.2, C52.2, C53.2, R37.2, R52.2, R54.2, U2.7 (PGND), U3.7 (PGND), U4.7 (PGND); also elsewhere on the board
unnamed: C15.1, D1.1 (K), U2.14 (BOOT)
unnamed: C17.1, D2.1 (K), U3.14 (BOOT)
unnamed: C19.1, D3.1 (K), U4.14 (BOOT)
unnamed: C51.1, R36.2, R37.1, U2.9 (CP-)
unnamed: C16.2, R1.1, U2.5 (DT)
unnamed: R40.1, R55.2, U2.2 (~SD/OD)
unnamed: C52.1, R51.2, R52.1, U3.9 (CP-)
unnamed: C18.2, R2.1, U3.5 (DT)
unnamed: R41.2, R56.2, U3.2 (~SD/OD)
unnamed: C53.1, R53.2, R54.1, U4.9 (CP-)
unnamed: C20.2, R3.1, U4.5 (DT)
unnamed: R42.2, R57.2, U4.2 (~SD/OD)
VCC: R36.1, R51.1, R53.1, R55.1, R56.1, R57.1; also elsewhere on the board

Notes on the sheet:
voltage sensing
gate drivers
note : in hwconf it needs to have #define INVERTED_BOTTOM_DRIVER_INPUT
external bootstrap optionnal for test Place only footprint
decoupling and bulk for drivers.
Need to add lowpass filter and check how sd/od really works (seems to be pulled high normally) Check the driver datasheet
input voltage will be up to 150v 240k and 5.1k looks good and can sense up to 158.6v
Hardware overcurrent should trip at about 1000a We are looking for the voltage drop on the shunt Vdr = Rshunt * current | therefore | Vdr = Rshunt * 1000 From Vdr we can calculate the resistor voltage divider ratio : Vdr = Vout = Vin * ratio | that is same as | ratio = Vin / Vdr = Vin / Rshunt * 10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

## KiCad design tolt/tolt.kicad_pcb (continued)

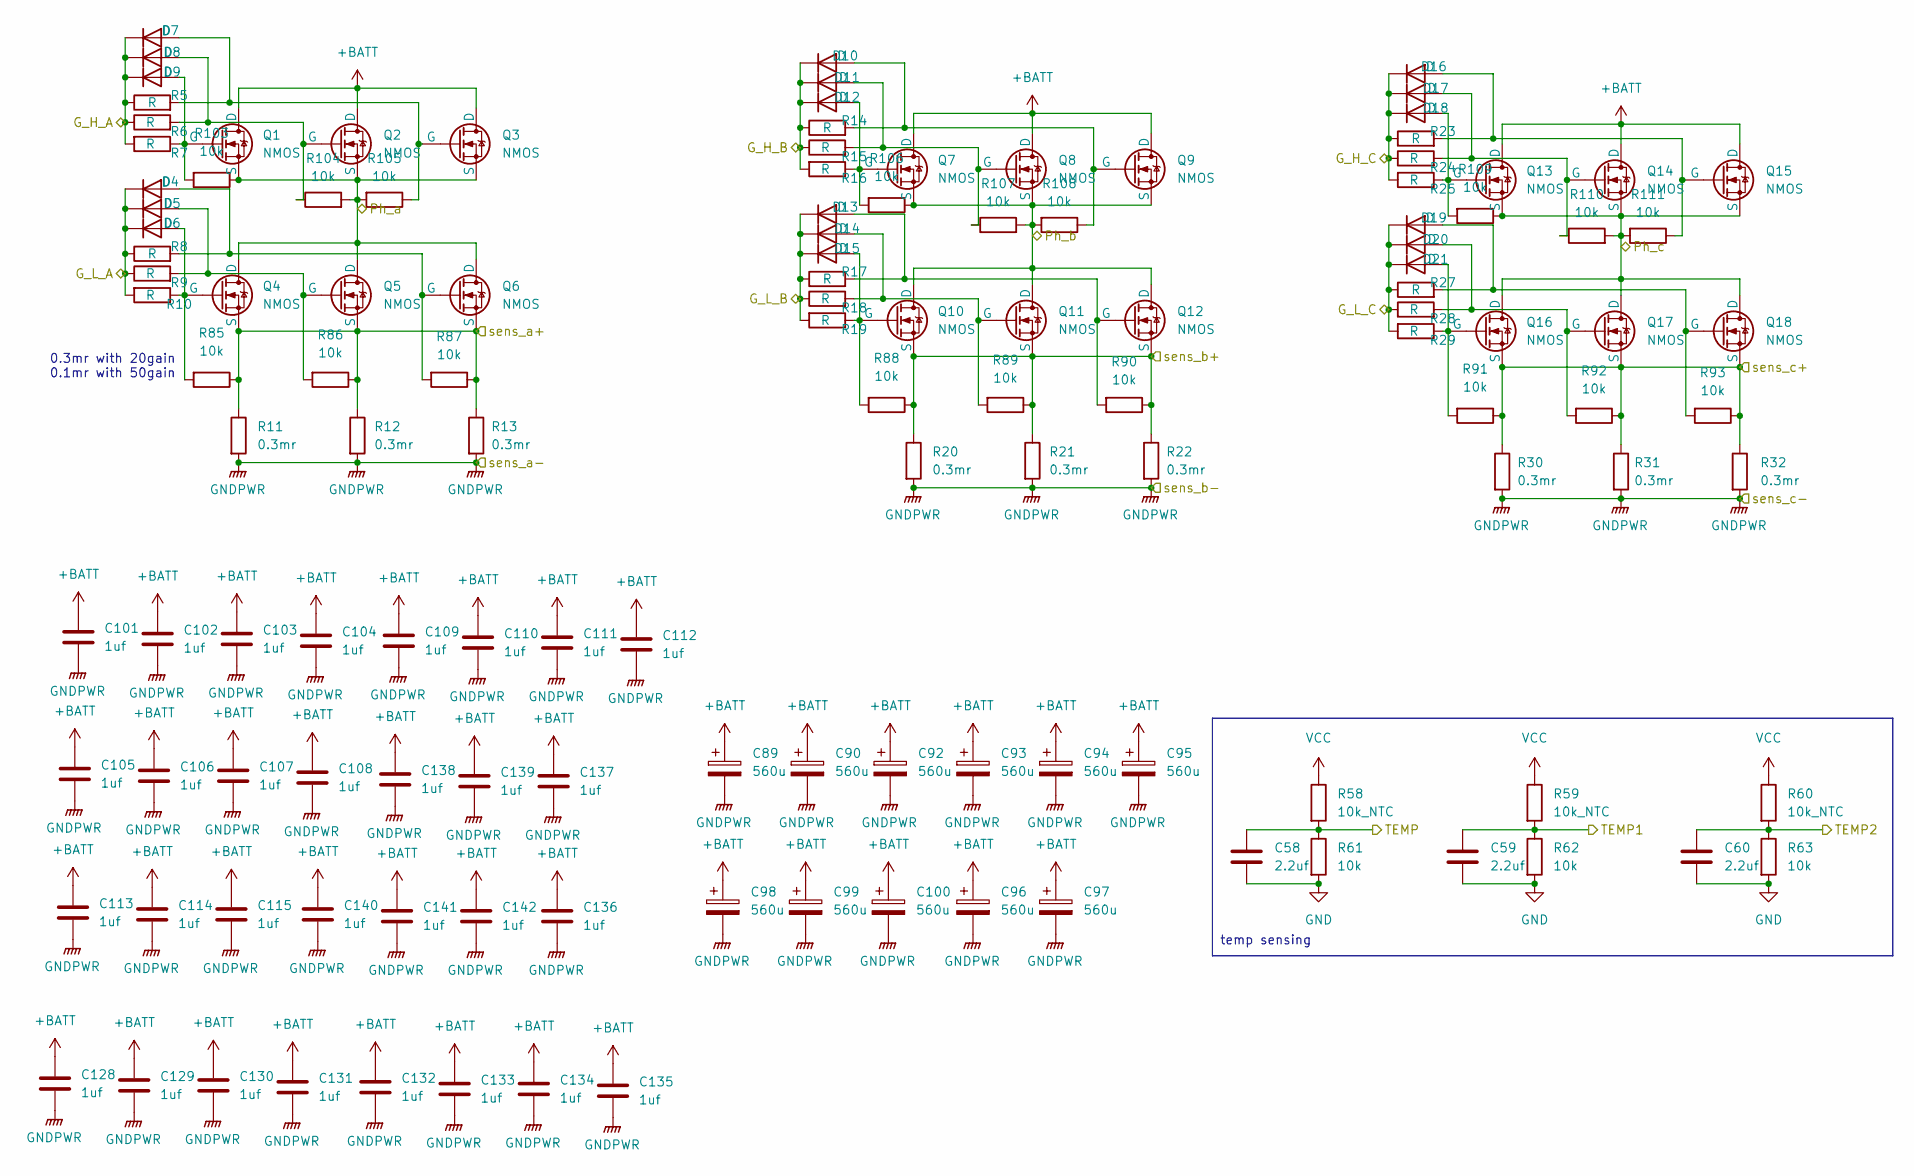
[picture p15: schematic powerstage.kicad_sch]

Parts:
C58, C59, C60: 2.2uf; C_0603_1608Metric
C89, C90, C92, C93, C94, C95, C96, C97, C98, C99, C100: 560u; CP_Radial_D16.0mm_P7.50mm
C101, C102, C103, C104, C105, C106, C107, C108, C109, C110, C111, C112, C113, C114, C115, C128, C129, C130, C131, C132, C133, C134, C135, C136, C137, C138, C139, C140, C141, C142: 1uf; C_2220_5750Metric_Pad1.97x5.40mm_HandSolder
D4, D5, D6, D7, D8, D9, D10, D11, D12, D13, D14, D15, D16, D17, D18, D19, D20, D21: D; D_SOD-123
Q1, Q2, Q3, Q4, Q5, Q6, Q7, Q8, Q9, Q10, Q11, Q12, Q13, Q14, Q15, Q16, Q17, Q18: NMOS; HDSOP-16-2
R5, R6, R7, R8, R9, R10, R14, R15, R16, R17, R18, R19, R23, R24, R25, R27, R28, R29: R; R_0805_2012Metric
R11, R12, R13, R20, R21, R22, R30, R31, R32: 0.3mr; R5930
R58, R59, R60: 10k_NTC; R_0603_1608Metric_Pad0.98x0.95mm_HandSolder
R61, R62, R63, R85, R86, R87, R88, R89, R90, R91, R92, R93, R103, R104, R105, R106, R107, R108, R109, R110, R111: 10k; R_0603_1608Metric

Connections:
+BATT: C89.1, C90.1, C92.1, C93.1, C94.1, C95.1, C96.1, C97.1, C98.1, C99.1, C100.1, C101.1, C102.1, C103.1, C104.1, C105.1, C106.1, C107.1, C108.1, C109.1, C110.1, C111.1, C112.1, C113.1, C114.1, C115.1, C128.1, C129.1, C130.1, C131.1, C132.1, C133.1, C134.1, C135.1, C136.1, C137.1, C138.1, C139.1, C140.1, C141.1, C142.1, Q1.1 (D), Q2.1 (D), Q3.1 (D), Q7.1 (D), Q8.1 (D), Q9.1 (D), Q13.1 (D), Q14.1 (D), Q15.1 (D); also elsewhere on the board
/INTER/G_H_A: D7.1 (K), D8.1 (K), D9.1 (K), R5.1, R6.1, R7.2; also elsewhere on the board
/INTER/G_H_B: D10.1 (K), D11.1 (K), D12.1 (K), R14.1, R15.1, R16.2; also elsewhere on the board
/INTER/G_H_C: D16.1 (K), D17.1 (K), D18.1 (K), R23.1, R24.1, R25.2; also elsewhere on the board
/INTER/G_L_A: D4.1 (K), D5.1 (K), D6.1 (K), R8.1, R9.1, R10.2; also elsewhere on the board
/INTER/G_L_B: D13.1 (K), D14.1 (K), D15.1 (K), R17.1, R18.1, R19.2; also elsewhere on the board
/INTER/G_L_C: D19.1 (K), D20.1 (K), D21.1 (K), R27.1, R28.1, R29.2; also elsewhere on the board
/INTER/Ph_a: Q1.3 (S), Q2.3 (S), Q3.3 (S), Q4.1 (D), Q5.1 (D), Q6.1 (D), R103.1, R104.2, R105.2; also elsewhere on the board
/INTER/Ph_b: Q7.3 (S), Q8.3 (S), Q9.3 (S), Q10.1 (D), Q11.1 (D), Q12.1 (D), R106.1, R107.2, R108.2; also elsewhere on the board
/INTER/Ph_c: Q13.3 (S), Q14.3 (S), Q15.3 (S), Q16.1 (D), Q17.1 (D), Q18.1 (D), R109.1, R110.2, R111.2; also elsewhere on the board
/INTER/SENS_A+: Q4.3 (S), Q5.3 (S), Q6.3 (S), R11.1, R12.1, R13.1, R85.1, R86.1, R87.1; also elsewhere on the board
/INTER/SENS_B+: Q10.3 (S), Q11.3 (S), Q12.3 (S), R20.1, R21.1, R22.1, R88.1, R89.1, R90.1; also elsewhere on the board
/INTER/SENS_C+: Q16.3 (S), Q17.3 (S), Q18.3 (S), R30.1, R31.1, R32.1, R91.1, R92.1, R93.1; also elsewhere on the board
/logic/ADC_T1: C58.1, R58.2, R61.1; also elsewhere on the board
/logic/ADC_T2: C59.1, R59.2, R62.1; also elsewhere on the board
/logic/ADC_T3: C60.1, R60.2, R63.1; also elsewhere on the board
GND: C58.2, C59.2, C60.2, R61.2, R62.2, R63.2; also elsewhere on the board
GNDPWR: C89.2, C90.2, C92.2, C93.2, C94.2, C95.2, C96.2, C97.2, C98.2, C99.2, C100.2, C101.2, C102.2, C103.2, C104.2, C105.2, C106.2, C107.2, C108.2, C109.2, C110.2, C111.2, C112.2, C113.2, C114.2, C115.2, C128.2, C129.2, C130.2, C131.2, C132.2, C133.2, C134.2, C135.2, C136.2, C137.2, C138.2, C139.2, C140.2, C141.2, C142.2, R11.2, R12.2, R13.2, R20.2, R21.2, R22.2, R30.2, R31.2, R32.2; also elsewhere on the board
unnamed: D4.2 (A), Q6.2 (G), R8.2, R87.2
unnamed: D5.2 (A), Q5.2 (G), R9.2, R86.2
unnamed: D6.2 (A), Q4.2 (G), R10.1, R85.2
unnamed: D7.2 (A), Q3.2 (G), R5.2, R105.1
unnamed: D8.2 (A), Q2.2 (G), R6.2, R104.1
unnamed: D9.2 (A), Q1.2 (G), R7.1, R103.2
unnamed: D10.2 (A), Q9.2 (G), R14.2, R108.1
unnamed: D11.2 (A), Q8.2 (G), R15.2, R107.1
unnamed: D12.2 (A), Q7.2 (G), R16.1, R106.2
unnamed: D13.2 (A), Q12.2 (G), R17.2, R90.2
unnamed: D14.2 (A), Q11.2 (G), R18.2, R89.2
unnamed: D15.2 (A), Q10.2 (G), R19.1, R88.2
unnamed: D16.2 (A), Q15.2 (G), R23.2, R111.1
unnamed: D17.2 (A), Q14.2 (G), R24.2, R110.1
unnamed: D18.2 (A), Q13.2 (G), R25.1, R109.2
unnamed: D19.2 (A), Q18.2 (G), R27.2, R93.2
unnamed: D20.2 (A), Q17.2 (G), R28.2, R92.2
unnamed: D21.2 (A), Q16.2 (G), R29.1, R91.2
VCC: R58.1, R59.1, R60.1; also elsewhere on the board

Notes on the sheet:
0.3mr with 20gain 0.1mr with 50gain
temp sensing

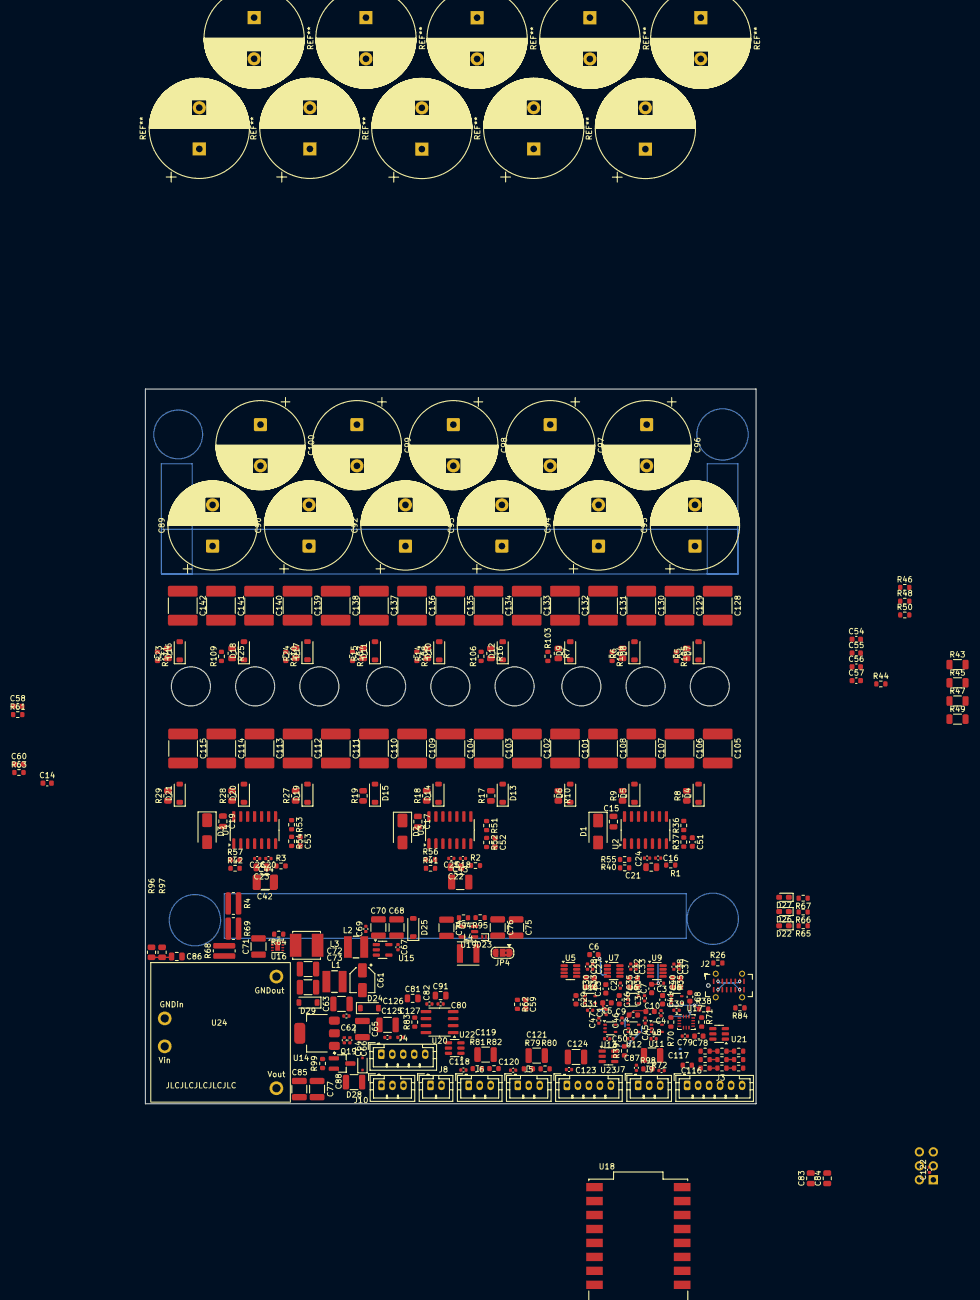
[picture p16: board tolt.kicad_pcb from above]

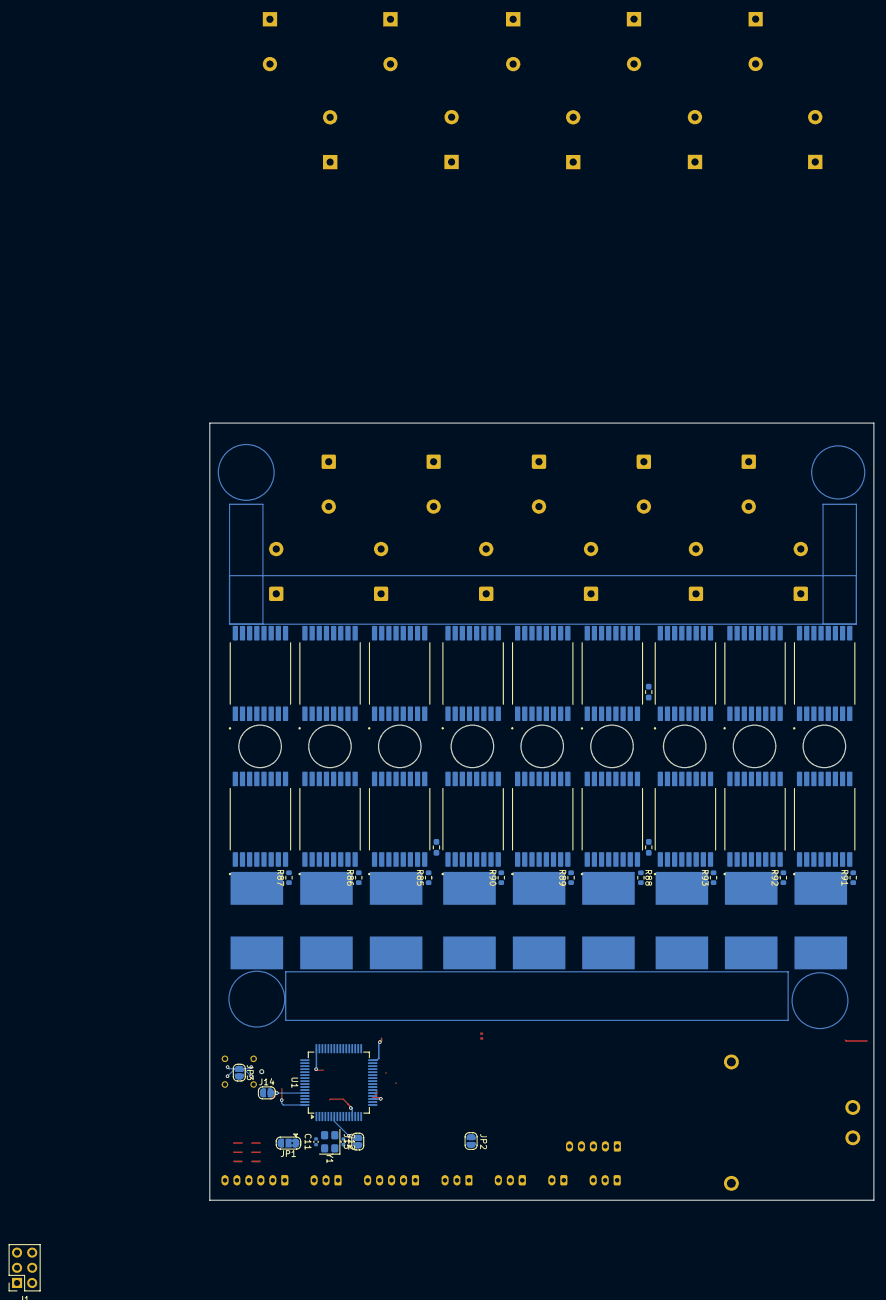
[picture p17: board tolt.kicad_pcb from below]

Board: 6 copper layers, 111.1 x 130.0 mm, 346 parts (49 on the bottom side), 131 nets.

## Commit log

2025-07-04 new file: tolt/desktop.ini new file: tolt/stm32.kicad_sch new file: tolt/tolt.kicad_pcb new file: tolt/tolt.kicad_pro new file: tolt/tolt.kicad_sch
    [stm32.kicad_sch, tolt.kicad_pcb, tolt.kicad_sch]
2025-07-04 new file: tolt/inter.kicad_sch modified: tolt/tolt.kicad_pro modified: tolt/tolt.kicad_sch
    [inter.kicad_sch]
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2025-07-05 modified: tolt/sheet.kicad_wks modified: tolt/tolt.kicad_pro modified: tolt/tolt.kicad_sch
    [tolt.kicad_sch]
2025-07-05 modified: tolt/inter.kicad_sch modified: tolt/stm32.kicad_sch
    [inter.kicad_sch, stm32.kicad_sch]
2025-07-05 new file: tolt/powerstage.kicad_sch modified: tolt/stm32.kicad_sch modified: tolt/tolt.kicad_pro modified: tolt/tolt.kicad_sch
    [powerstage.kicad_sch, stm32.kicad_sch, tolt.kicad_sch]
2025-07-05 modified: tolt/inter.kicad_sch modified: tolt/powerstage.kicad_sch
    [inter.kicad_sch, powerstage.kicad_sch]
2025-07-06 i hate RC Filters
    [inter.kicad_sch, stm32.kicad_sch]
2025-07-06 modified: tolt/inter.kicad_sch modified: tolt/stm32.kicad_sch modified: tolt/tolt.kicad_sch
    [inter.kicad_sch, stm32.kicad_sch, tolt.kicad_sch]
2025-07-06 modified: tolt/inter.kicad_sch modified: tolt/powerstage.kicad_sch modified: tolt/stm32.kicad_sch modified: tolt/tolt.kicad_sch
    [inter.kicad_sch, powerstage.kicad_sch, stm32.kicad_sch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]
2025-07-07 new file: ESP32-C3_SUPERMINI_SMD.step new file: tolt/Library.pretty/MODULE_ESP32-C3_SUPERMINI.kicad_mod new file: tolt/auxl.kicad_sch
    [ESP32-C3_SUPERMINI_SMD.step, auxl.kicad_sch]
2025-07-08 modified: tolt/converters.kicad_sch modified: tolt/inter.kicad_sch modified: tolt/stm32.kicad_sch modified: tolt/tolt.kicad_pcb modified: tolt/tolt.kicad_pro modified: tolt/tolt.kicad_sch
    [converters.kicad_sch, inter.kicad_sch, stm32.kicad_sch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]
2025-07-08 modified: tolt/auxl.kicad_sch modified: tolt/converters.kicad_sch modified: tolt/powerstage.kicad_sch modified: tolt/stm32.kicad_sch modified: tolt/tolt.kicad_pcb modified: tolt/tolt.kicad_pro modifi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
    [auxl.kicad_sch, converters.kicad_sch, powerstage.kicad_sch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]
2025-07-08 new file: SOP120P1500X235-17N.step new file: tolt/Library.pretty/HDSOP-16-2.kicad_mod new file: tolt/Library.pretty/R5930.kicad_mod new file: tolt/conn.kicad_sch
    [SOP120P1500X235-17N.step, conn.kicad_sch]
2025-07-09 Revert "Merge branch 'main' of https://github.com/LJBoxx/bigtolt"
    This reverts commit 648dc93627ac55c8b54fa74faadbb35a312ea564, reversing
    changes made to 972c1c2491e13322900779e00755fdd65e6f8c8a.
    [SOP120P1500X235-17N.step, auxl.kicad_sch, conn.kicad_sch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]
2025-07-09 Reapply "Merge branch 'main' of https://github.com/LJBoxx/bigtolt"
    This reverts commit 10d1035653869a11abcc4dc45a35a471baa73785.
    [SOP120P1500X235-17N.step, auxl.kicad_sch, conn.kicad_sch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]
2025-07-09 revert the mess
    i am stupid
    [auxl.kicad_sch, converters.kicad_sch, tolt.kicad_pcb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]
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2025-07-11 new file: tolt/Library.pretty/IND-SMD_L3.9-W3.9-1.kicad_mod new file: tolt/Library.pretty/IND-SMD_L5.0-W5.0.kicad_mod modified: tolt/auxl.kicad_sch modified: tolt/conn.kicad_sch modified: tolt/conver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
    [auxl.kicad_sch, conn.kicad_sch, converters.kicad_sch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]
2025-07-11 modified: tolt/converters.kicad_sch modified: tolt/inter.kicad_sch modified: tolt/tolt.kicad_sch
    [converters.kicad_sch, inter.kicad_sch, tolt.kicad_sch]
2025-07-11 new file: tolt/Library.pretty/PQDE6W.kicad_mod modified: tolt/auxl.kicad_sch modified: tolt/conn.kicad_sch modified: tolt/converters.kicad_sch modified: tolt/powerstage.kicad_sch modified: tolt/tolt.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
    [auxl.kicad_sch, conn.kicad_sch, converters.kicad_sch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]
2025-07-12 modified: tolt/conn.kicad_sch modified: tolt/converters.kicad_sch modified: tolt/inter.kicad_sch modified: tolt/powerstage.kicad_sch modified: tolt/stm32.kicad_sch modified: tolt/tolt.kicad_pcb modif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
    [conn.kicad_sch, converters.kicad_sch, inter.kicad_sch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]
2025-07-13 modified: tolt/conn.kicad_sch modified: tolt/powerstage.kicad_sch modified: tolt/stm32.kicad_sch modified: tolt/tolt.kicad_pcb modified: tolt/tolt.kicad_pro modified: tolt/tolt.kicad_sch
    [conn.kicad_sch, powerstage.kicad_sch, stm32.kicad_sch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]
2025-07-14 Update PCB component placements and replace jumper
    Moved several SMD components to new coordinates for layout optimization. Removed J14 (BOOT0 solder jumper) and added JP4 (3-pad solder jumper) for converter section. Updated silkscreen and fab UUIDs for multiple components.
    [tolt.kicad_pcb]
2025-07-14 modified: tolt/conn.kicad_sch modified: tolt/tolt.kicad_pcb modified: tolt/tolt.kicad_pro
    [conn.kicad_sch]
2025-07-17 modified: tolt/stm32.kicad_sch modified: tolt/tolt.kicad_pcb modified: tolt/tolt.kicad_pro modified: tolt/tolt.kicad_sch
    [stm32.kicad_sch, tolt.kicad_sch]
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2025-07-31 converter edit
    2x ltc7137
    [converters.kicad_sch]
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2025-08-08 modified: tolt/converters.kicad_sch modified: tolt/tolt.kicad_pcb
    [converters.kicad_sch]
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2025-09-24 some fixed and edit
    tbd : phase voltage sensing and adct1 wiring and add on/off switch
    [converters.kicad_sch, inter.kicad_sch]
2025-09-25 added conn for aux 12v
    more tbd : add test points
    [converters.kicad_sch]
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2025-10-30 sch cleanup
    cleaned fet sheet and added ferrite bead
    Fixed some ground issues
    [powerstage.kicad_sch]
2025-11-02 finished routing
    AAAAAAAAAAAAAAAAaaAAAAAAAAAAAAAAAAaaAAAAAAAAAAAAAAAAaaAAAAAAAAAAAAAAAAaaAAAAAAAAAAAAAAAAaaAAAAAAAAAAAAAAAAaaAAAAAAAAAAAAAAAAaaAAAAAAAAAAAAAAAAaaAAAAAAAAAAAAAAAAaaAAAAAAAAAAAAAAAAaaAAAAAAAAAAAAAAAAaa
    PLZ WORK PLZ WORK PLZ WORK PLZ WORK PLZ WORK PLZ WORK PLZ WORK PLZ WORK PLZ WORK PLZ WORK PLZ WORK PLZ WORK PLZ WORK PLZ WORK PLZ WORK PLZ WORK PLZ WORK PLZ WORK PLZ WORK PLZ WORK PLZ WORK PLZ WORK P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
    [converters.kicad_sch, powerstage.kicad_sch]
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2025-11-17 big update
    fixed decoupling correctly
    more gnd plane work and routing finished
    [converters.kicad_sch, inter.kicad_sch, powerstage.kicad_sch]
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2025-12-13 more assign+12-5v change
    changed with TPS82130
    Since using esp32 will increase consumption by a lot
    [auxl.kicad_sch, conn.kicad_sch, converters.kicad_sch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]
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2025-12-21 Done
    hopefully finished ?
    needs sanity check and more checks
    [conn.kicad_sch, converters.kicad_sch, inter.kicad_sch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]
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
